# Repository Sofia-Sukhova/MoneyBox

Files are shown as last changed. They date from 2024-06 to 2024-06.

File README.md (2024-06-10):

# MoneyBox :coin: 
### Команда

Бочкарев Федор - электроника и ПО

Бочкарева Софья - проектирование и 3D моделирование

## Цель
Построить копилку с автоматическим определением номинала монет и накоплением общей суммы.

## Решение
Корпус копилки состоит из двух частей - короба для монет и крышки, на которой закреплены все основные детали механизма.

Общая схема определения номинала монеты: монета попадает в щель монетоприемника и перекрывает инфракрасный сигнал светодиода, управляющий фототранзистором. Фототранзистор посылает сигнал на шаговый мотор, присоединенный к клину, закрывающему щель монетоприемника.
Клин отводится на расстояние, соответствующее заданным номиналам монеты, и как только монета падает в щель, фоторанзистор получает сигнал инфракрасного светодиода. Так определяется номинал монеты.

Визуализация данных осуществляется с помощью 4-х строчного дисплея в двух режимах, которые переключаются кнопкой: отображение общей суммы и отображение распределения по номиналам. Также предусмотрен сброс суммы в ноль с помощью кнопки reset. 

Питание осуществляется от сети постоянного тока 5V 

### Компоненты и технологии

* Корпус, крышка и детали механизма затвора (клин-задвижка и поворотное кольцо) напечатаны из PETG пластика на 3D принтере.

* Для электрической части использованы 
  * Arduino Nano
  * Шаговый мотор
  * LCD дисплей 2004 с модулем I2C 
  * плата-драйвер мотора
  * фототранзистор
  * ИК светодиод

### Проблемы и трудности

Основная проблема заключалась в ошибках проектирования корпуса и крышки, которые были выявлены во время тестирования устройства.

## Тестирование устройства

https://github.com/Sofia-Sukhova/MoneyBox/assets/80464142/ff9c0ffd-643b-4358-b3ea-821b1e63e1c1

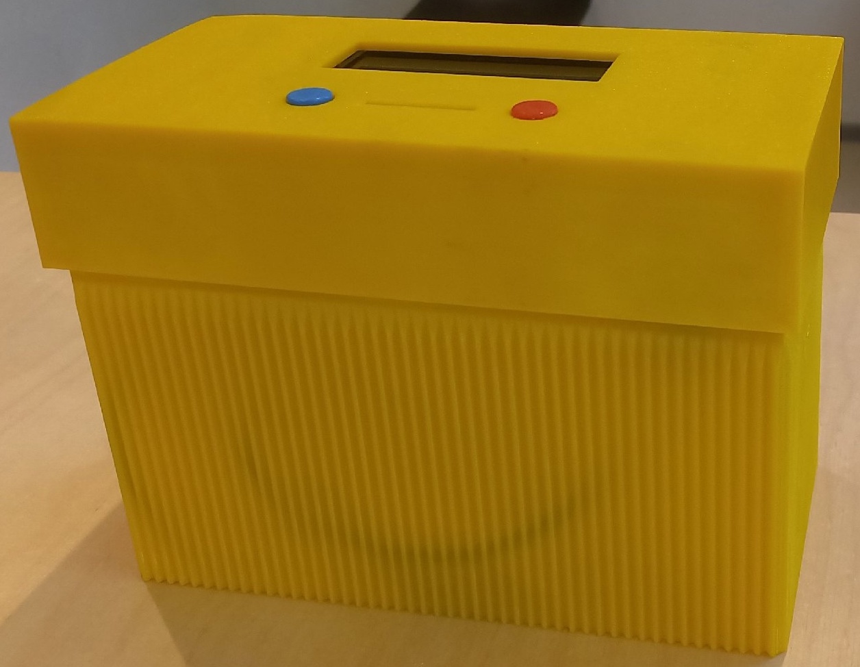
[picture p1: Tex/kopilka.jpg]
Фото готовой копилки снаружи


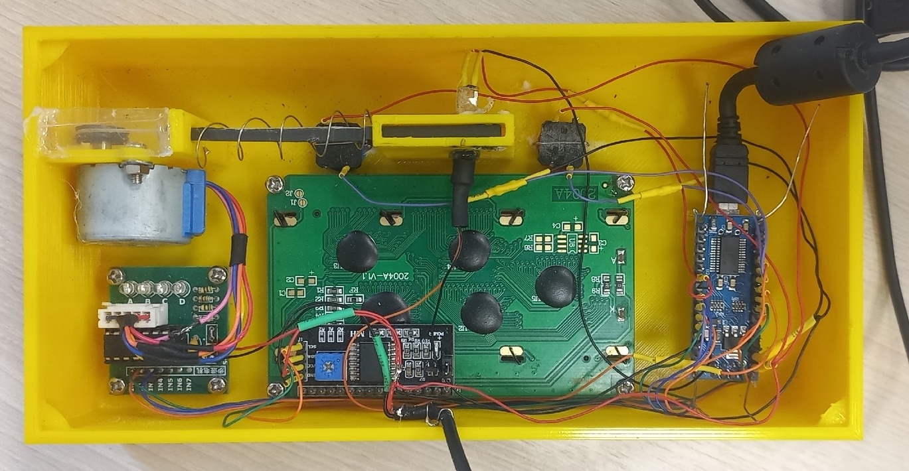
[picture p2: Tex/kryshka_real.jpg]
Фото готовой копилки внутри


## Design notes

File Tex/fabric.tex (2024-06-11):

\subsection{Изготовление и сборка.}

Все детали были изготовлены на 3д принтере. Изначально коробка была сделана без ребер жесткости, из-за чего при печати она деформировалась. Поэтому мы изменили конструкцию коробки, добавив ребра жесткости. 
\par\medskip

\begin{figure}[H]
	\centering
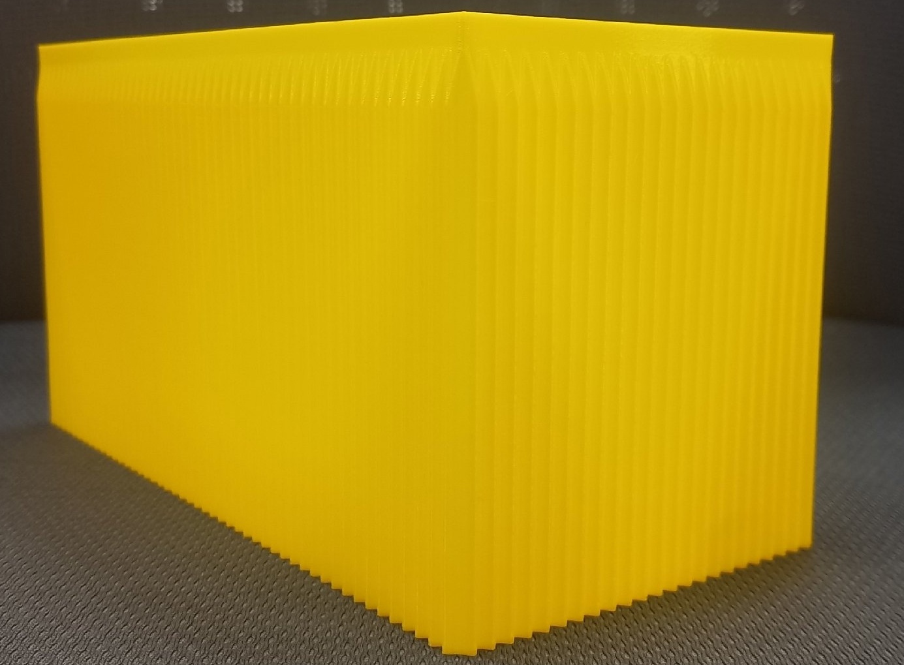
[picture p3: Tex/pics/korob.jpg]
	
	\caption{Короб для монет}
	\label{ris:korob_done}
\end{figure}

Электрическая схема была собрана из: шагового мотора, платы-драйвера шагового мотора, Arduino Nano, фототранзистора, ИК-светодиода, LCD экрана формата 2004 вместе с платой I2C, 2-х кнопок и провода USB (для питания). Схема соединений приведена ниже на рисунке~\ref{ris:scheme_electric}.

\begin{figure}[H]
	\centering
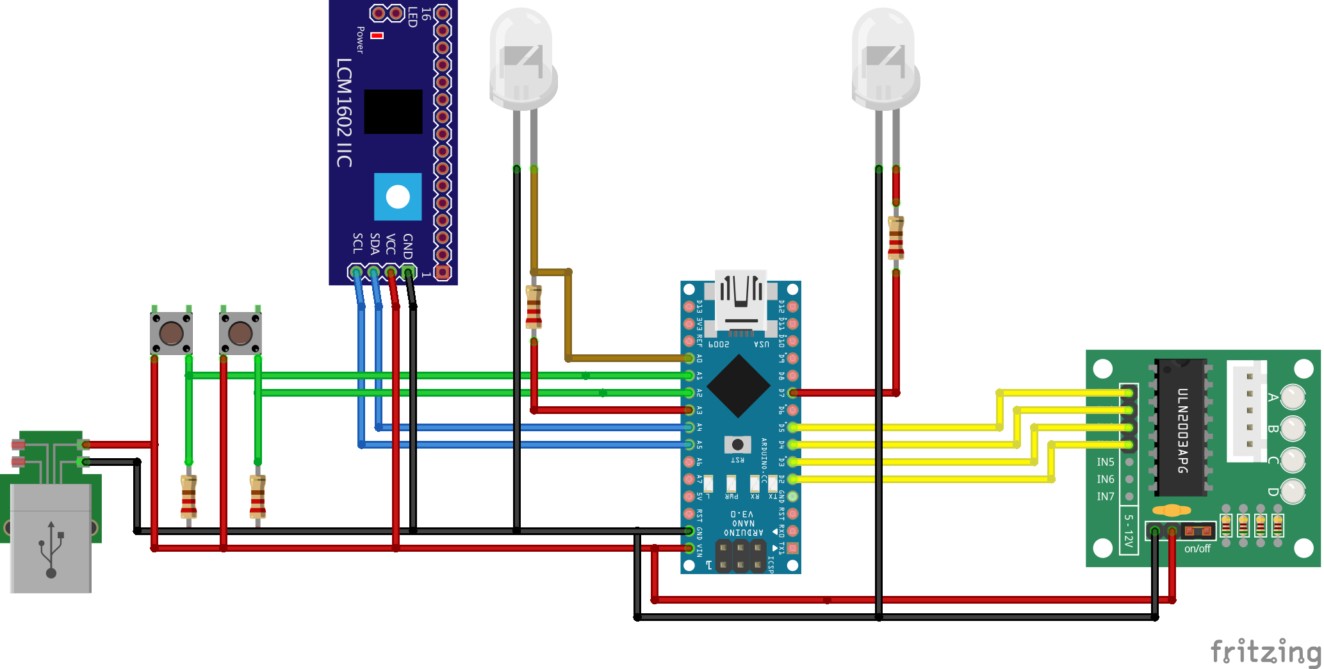
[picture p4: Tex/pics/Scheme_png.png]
	
	\caption{Схема соединения проводов}
	\label{ris:scheme_electric}
\end{figure}

При сборке были исправлены выявленные ошибки моделирования. В основном это касается отсутствующего отверстия для щели под ИК-светодиод и фототранзистор.
\par\medskip

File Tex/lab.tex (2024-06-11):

\documentclass[a4paper,12pt]{extarticle}	% Стиль
%\usepackage[pdftex,unicode,colorlinks=true,linkcolor = blue]{hyperref}

\usepackage{graphicx}
\usepackage{wrapfig}

\usepackage{rotating}

\usepackage{mathtext}
%\usepackage{autonum}

\usepackage{multirow}

\usepackage{caption}

\usepackage{float}

\usepackage{enumitem}
\usepackage{hyperref}
\usepackage[rgb]{xcolor}
\hypersetup{ % Гиперссылки
	colorlinks=true, % false: ссылки в рамках
	urlcolor=blue, % на URL
    linkcolor=blue,
	citecolor=blue,
    filecolor=blue 
}

\usepackage[T2A]{fontenc}
\usepackage[utf8]{inputenc}
\usepackage[english,russian]{babel}

\usepackage{amsmath,amsfonts,amssymb,amsthm,mathtools}

\usepackage{indentfirst} % Красная строка

\newenvironment{comment}{}{}

\graphicspath {{ Images / }}

\usepackage{listings}             % Include the listings-package
\lstset{language=[ANSI]C}
\lstset{numbers=left, stepnumber=1}

\bibliographystyle{gost-numeric.bbx}
\usepackage[hyperref=true,bibencoding=utf8,bibstyle=gost-numeric,sorting=none]{biblatex}
\addbibresource{refs.bib}
\DeclareFieldFormat{url}{\href{#1}{\mkbibacro{URL}}}

\usepackage[left=2cm,right=2cm,top=2cm,bottom=2cm]{geometry}

\begin{document}

	\begin{titlepage}
	\begin{center}
	Физтех-фабрика\\
	\vspace*{5cm}

	\section*{Копилка с автоматическим счётчиком монет}

	\begin{minipage}{0.3\textwidth}
	~
	\end{minipage}
	\hfill
	\begin{minipage}{0.2\textwidth}
		Выполнили:
	\end{minipage}
	\begin{minipage}{0.4\textwidth}
		Бочкарев Федор, Б01-003\\
		Бочкарева Софья, Б01-003
	\end{minipage}

	\begin{flushright}\textbf{\\}\end{flushright}

	\vfill

	Московский физико-технический институт\\
	\the\year{} год

	\end{center}
	\end{titlepage}

	\parindent=0cm
	\parskip=1pt
	\reversemarginpar
	\marginparpush = 0 pt

	\input{intro.tex}
	\input{project.tex}
	\input{fabric.tex}
	\input{progr.tex}
	\input{result.tex}
	\input{links.tex}

\end{document}

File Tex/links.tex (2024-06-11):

\printbibliography[heading=bibnumbered, title=Ссылки.]

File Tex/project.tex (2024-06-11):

\section {Проектирование и изготовление.}

Основные этапы работы:

\begin{itemize}
	\item Проектирование и прототипирование; 
	\item Изготовление деталей;
	\item Сборка;
	\item Разработка управляющей программы
\end{itemize}

\subsection{Проектирование и прототипирование.}

\begin{figure}[H]
	\centering
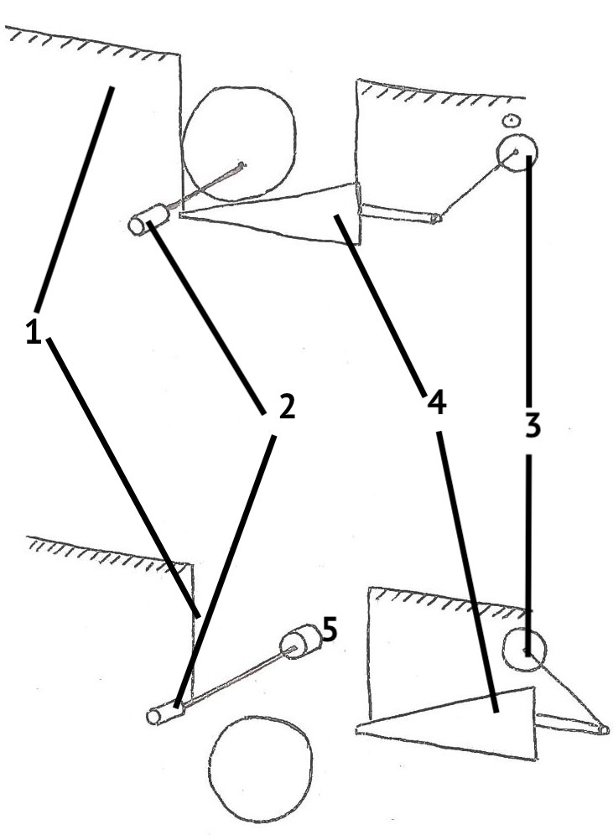
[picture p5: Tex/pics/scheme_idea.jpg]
	
	\caption{Принципиальная схема устройства}
	\label{ris:scheme_idea}
\end{figure}
\par\medskip

Принципиальная схема устройства приведена на рис.~\ref{ris:scheme_idea}. Монета падает в щель монетоприемника 1 и перекрывает инфракрасный луч от инфракрасного светодиода 2. Фоторанзистор 5 передает управляющий сигнал на шаговый мотор 3, который приводит в движение клин 4. Когда клин отводится достаточно для того, чтобы монета упала насквозь, инфракрасный луч светодиода 2 перестает перекрываться, что фиксируется фототранзистором. 
\par\medskip

По данной принципиальной схеме был собран прототип (см. рис.~\ref{ris:proto}). Он успешно прошел проверку на работоспособность, что позволило нам использовать данный механизм в дальнейшем.

\begin{figure}[H]
	\centering
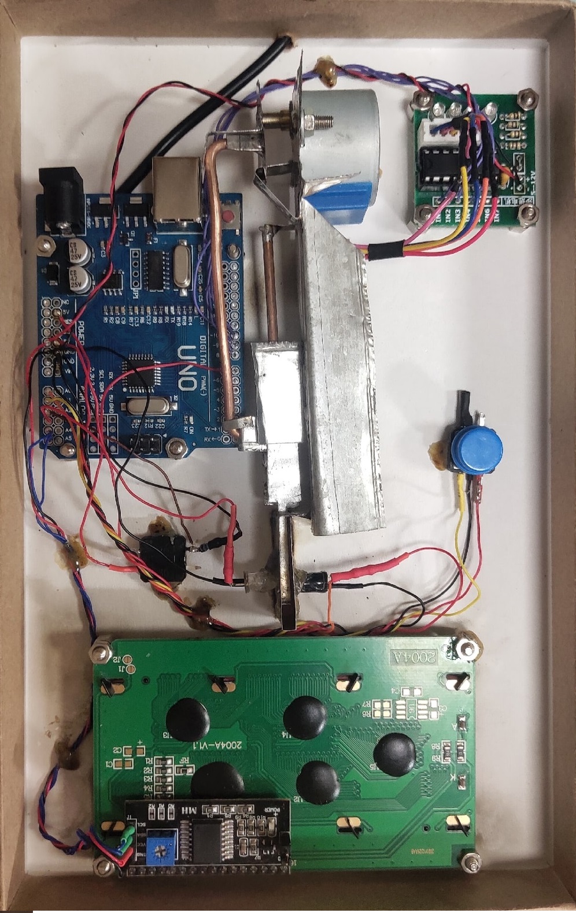
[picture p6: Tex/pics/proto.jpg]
	
	\caption{Прототип}
	\label{ris:proto}
\end{figure}
\par\medskip

При проектировании финальной версии мы доработали механизм затвора для его длины (со 120 мм до 60 мм) (см. рис.~\ref{ris:mechan}). Корпус копилки состоит из двух основных составных частей - крышки, на которой закреплены все основные детали механизма, и коробки для монет. 

\begin{figure}[H]
	\centering
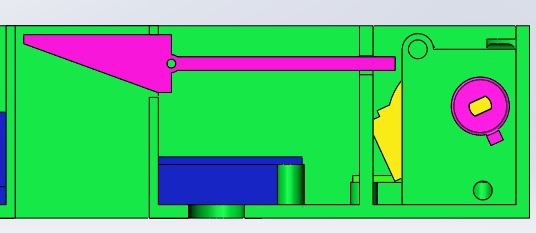
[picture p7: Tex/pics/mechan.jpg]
	
	\caption{Реализация механизма}
	\label{ris:mechan}
\end{figure}
\par\medskip

На верхней крышке предусмотрено размещение 2-х кнопок, дисплея, модуля Arduino Nano, драйвера шагового мотора и его драйвера, фототранзистора и инфракрасного светодиода и механизма затвора. Питание осуществляется от постоянного тока 5V от сети (см. рис.~\ref{ris:kryshka_model}, рис.~\ref{ris:kryshka_real}).  

\begin{figure}[H]
	\centering
	
	\caption{Крышка -- реализация}
	\label{ris:kryshka_real}
\end{figure}
\par\medskip

\begin{figure}[H]
	\centering
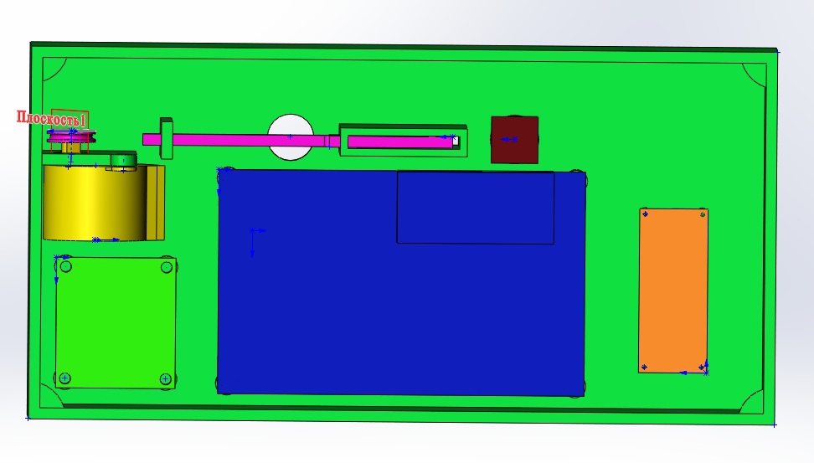
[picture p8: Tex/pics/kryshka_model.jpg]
	
	\caption{Крышка -- модель}
	\label{ris:kryshka_model}
\end{figure}
\par\medskip

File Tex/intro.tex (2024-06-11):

\section {Введение.}

На сегодняшний день большинство транзакций и расчётов происходит путём переводов из мобильных приложений, либо по бесконтактной оплате. Несмотря на рост безналичных платежей, мелкие монеты все еще остаются частью повседневных расчетов. Накоплениеи мелочи может мешать людям своим неопределённым положением -- мелочь лежит где-то на столе, в различных кармах. Организация копилки определит конкретное место для скопившейся мелочи и поможет вернуть её в оборот.
\par\medskip

Исходя из этих соображений, была выдвинута цель.

\section{Цель.}

Построить копилку с автоматическим определением номинала монет и накоплением общей суммы.

\subsection*{Задачи:}
\begin{itemize}
	\item Анализ существующих решений;
	\item Проектирование и изготовление устройства;
	\item Проверка и верификация надёжности работы
\end{itemize}

\section {Анализ существующих аналогов.}

Основными способами определять номинал монеты является определение одного из трёх характерных параметров: диаметр, толщина или магнитные свойства. 
\par\medskip

Определение номинала по магнитным свойствам возможно только с очень чувствительными (дорогими) датчиками.
\par\medskip

Определение номинала по толщине требует высокой точности -- до 0,01 мм. К тому же монета 50 копеек и 1 рубль имеют одинаковую толщину, что делает невозможным одновременный счёт в одном устройстве и копеек и рублей.
\par\medskip

Разница в диаметре различных монет составляет минимум 1 мм. Поэтому реализовать механизм определения номинала монеты целесообразнее именно по диаметру.
\par\medskip

Копилки со счетчиками монет не являются чем-то новым, они уже продаются в различных вариациях, однако такие устройства либо не являются автоматическими и требуют ручного ввода добавленной суммы (пример \cite{Ozon_manual_work}); либо их цена сильно завышена \cite{Ali_auto_work} (стоит отметить, что всевозможные конструкционные решения уже реализованны в широком классе устройств \cite{Cassida}, \cite{Sort_Cassida}, которые специализируются на крупном монетно/денежном обороте, что характерно для банковского сектора, предпринимателей).
\par\medskip

Помимо счётчиков, существуют ещё сортировщики монет, которые достаточно быстро разделяют монеты по номиналу на разные отсеки (примеры: \cite{Sort_Cassida},\cite{Sort_hill},\cite{Sort_default}). Все они имеют схожий механизм работы: монеты скатываются по определённой дорожке и разделяются в процессе движения. Любой подобный сортировщик можно модернизировать: добавить датчики на обнаружение проскакивания монеты на каждый из отсеков разделения и соединить все эти датчики с счётчиком монет -- получится необходимая нам копилка. К сожелению, все подобные сортировщики имеют большие размеры, что является недостатком -- копилка не должна занимать много места.
\par\medskip

Наиболее подходящим будет являтся пример устройста \cite{Gyver} -- диаметр определяется по интенсивности инфракрасного сигнала, приходящего на фоточувствительный элемент (фототранзистор); монеты перекрывают часть ИК-излучения и это изменение регистрирует датчик. Такая реализация допускает возможность ошибки за счет проскакивания монеты и неправильного считывания ее диаметра (к тому же в этой версии не предусмотрены удобные элементы управления).
\par\medskip

\section {Общее описание.}

Исходя из анализа существующих решений, можно составить требования к нашей копилке-счётчику: без сортировки, только автоматический счёт, высокая надёжность, низкая вероятность ошибки, компактность, удобство использования, хороший дизайн.
\par\medskip

Основу надёжного механизма будет составлять не просто щель, а щель с внутренней задвижкой -- такая конструкция не допустит проскакивания монеты без корректного считывания. К тому же, основным измерительным устройством в копилке будет сама щель с задвижкой -- отклонившись на определённую величину, через задвижку проскочат только те монеты, диаметр которых меньше этой величины. Расширяя щель поочерёдно от меньшего диаметра к большему, на каждом отколнии можно определить прошла ли монета или нет, и, в зависимости от итогового отклонения, определять какой был номинал у выпавшей монеты.
\par\medskip

За движение задвижки будет отвечать шаговый мотор. Тем самым, измерение с какого-либо датчика перекладывается на установление заданного угла шагового мотора. Фототранзистор и ИК-светодиодом также установлены в щель -- их задача определять, есть ли в щели монета. Именно фототранзистор и ИК-светодиод будут задавать начало измерения номинала монеты и постепенное открытие щели, а также поределять момент проскакивания монеты при открывании щели.
\par\medskip

Для удобства эксплуатации данные о принятых монетах выводятся на дисплей в двух режимах: общая сумма в копилке и распределение содержимого по номиналам. Управление копилкой осуществляется через 2 кнопки.
\par\medskip

Питание всей электроники осуществело от 5 вольт постоянного тока по кабелю USB.

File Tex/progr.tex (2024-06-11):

\subsection{Разработка управляющей программы.}

Основу прошивки Arduino Nano составляют добавленные библиотеки.

\begin{lstlisting}[frame=single]
#include <GyverStepper.h>
#include <EEPROM.h>
#include <PinChangeInterrupt.h>
#include <string.h>
#include <LiquidCrystal_I2C.h>
\end{lstlisting}

В дальнейшем, весь код можно разделить на части:

\begin{itemize}
	\item Объявление констант, классов, переменных и дефайнов;
	\item Основная работа;
	\item Функции/код связанные с экраном и его выводом;
	\item Функции связанные с записью количества монет в энергонезависимую EEPROM память;
	\item Обработка клафиш управления
\end{itemize}

Вся основная работа заключена в простой алгоритм: постоянно считывается данные с сенсора (фототранзистора), если они превысили определенный порог (сенсор заслонили от ИК), то у нас монетка и нужно отодвигать защёлку путём поворота шагового мотора. Для каждой монетки существует соответствующий угол, который напрямую связан с диаметром монеты. Зная на каком углу датчик вновь увидел ИК мы можем определить какая это монета.

\begin{lstlisting}[frame=single]
void loop {
	data = analogRead();
	if (data > BORDER) {
		if      (check(...)){this_coin = 0}
		else if (check(...)){this_coin = 1}
		...
	}
}
\end{lstlisting}

Из вышеприведённой вставки, главная функция имеет следующий функционал: поворачивается на определённый угол $R$, затем даёт время на возможный сброс монетки и срабатывание датчика $Y$, потом вновь считывает датчик и определяет -- упала ли монета или нет. 
\par\medskip

\begin{lstlisting}[frame=single]
bool check(int * mass, int R, int Y){
	int data = analogRead(inSEN);
	if (data > 100) {
		my_rotate(R);
	} else {
		comeback();
		return 1;
	}
	delay(Y);
	return 0;
}
\end{lstlisting}
Если монета была сброшена, то эта функция прорутит мотор до стопора, тем самым вернув защёлку в полностью закрытое состояние.
\par\medskip

По результату выхода из этой функции определяется тип монетки и он записывается в буффер имеющихся монет.
\par\medskip

По данным этого буффера на экран выводиться сумма и количество монет по номиналам.
\par\medskip

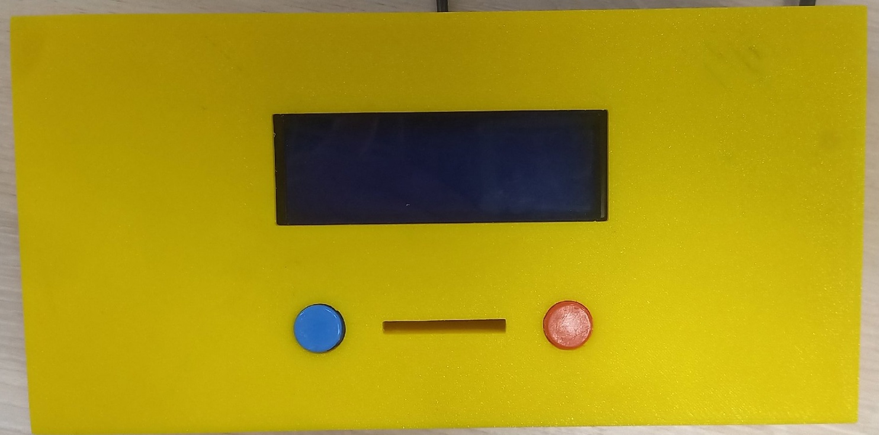
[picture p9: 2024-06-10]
Tex/pics/kryshka_face_real.jpg

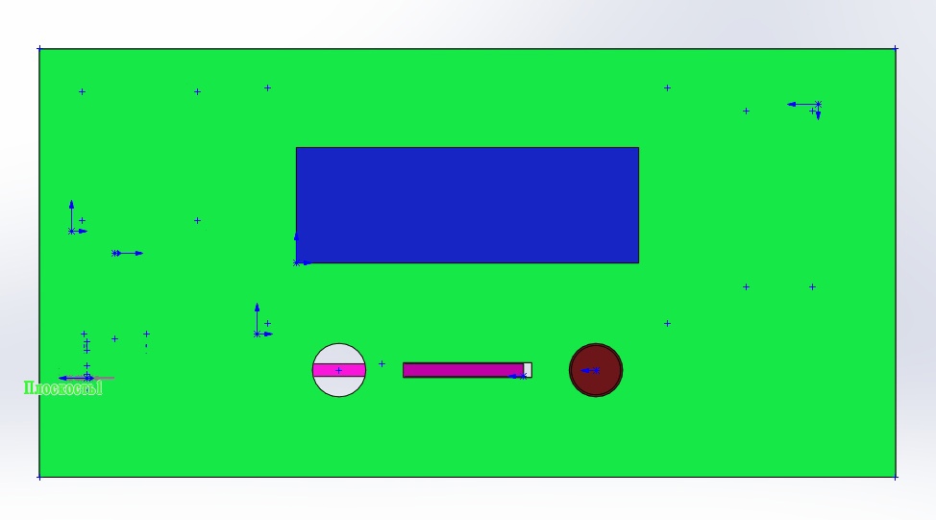
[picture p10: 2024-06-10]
Tex/pics/kryshka_face_model.jpg

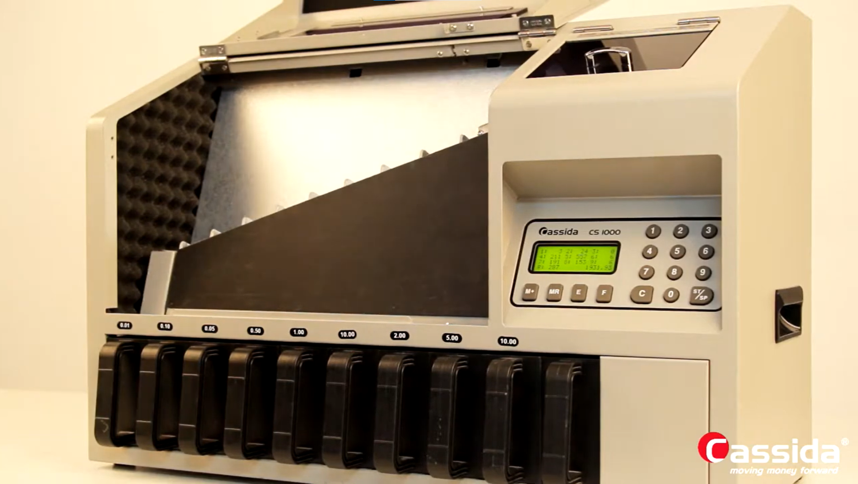
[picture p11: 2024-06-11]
Tex/pics/Cassida_sorting.png

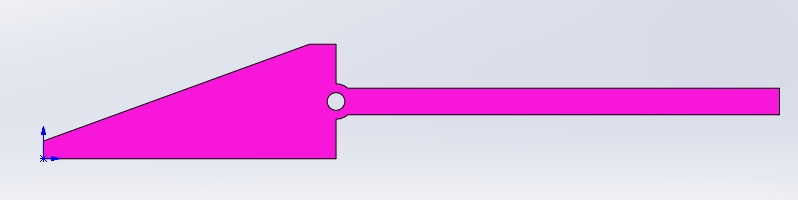
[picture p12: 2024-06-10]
Tex/pics/klin.jpg

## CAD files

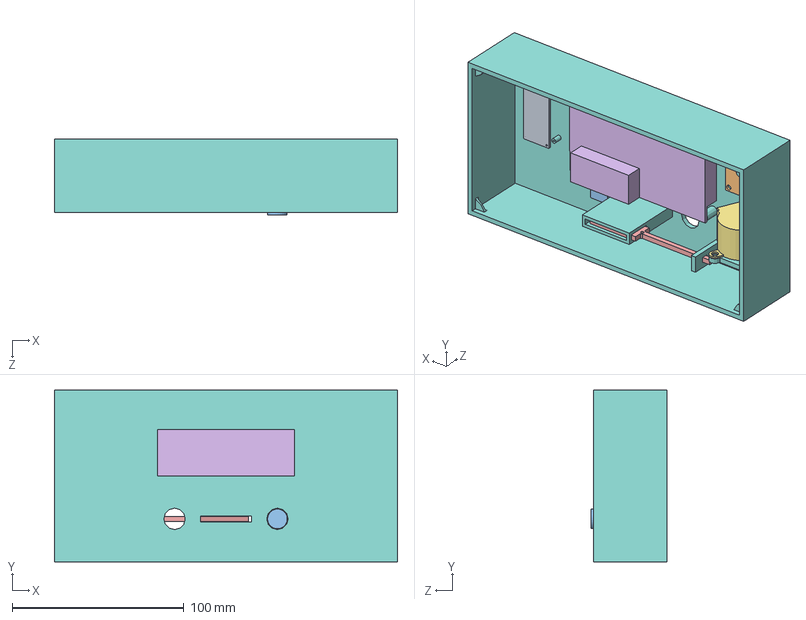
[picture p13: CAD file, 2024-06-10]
CAD/Сборка.SLDASM
200.0 x 100.0 x 44.5 mm
Крышка
Мотор
Экран
Клин
Колечко
Кнопка
Плата-драйвер
Плата-ардуино

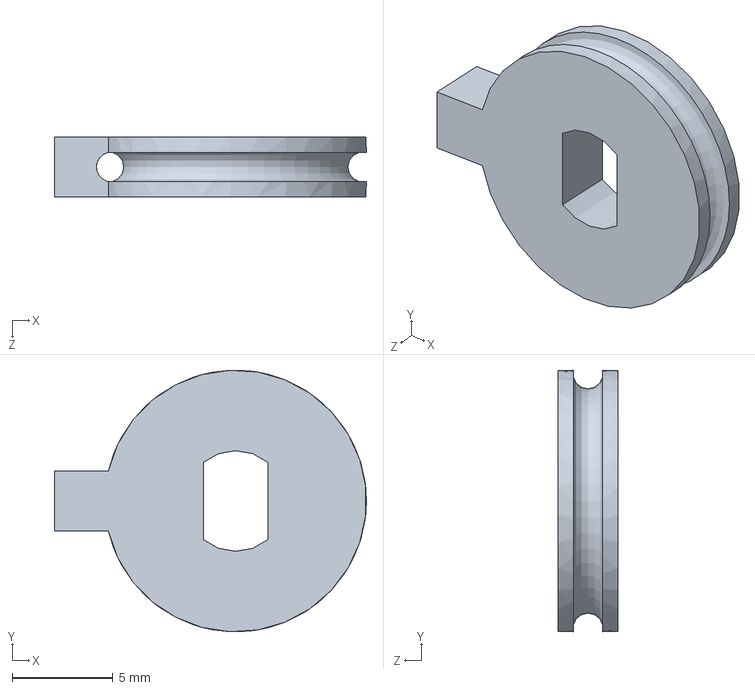
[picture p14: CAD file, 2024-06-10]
CAD/Колечко.SLDPRT
15.5 x 13.0 x 3.00 mm

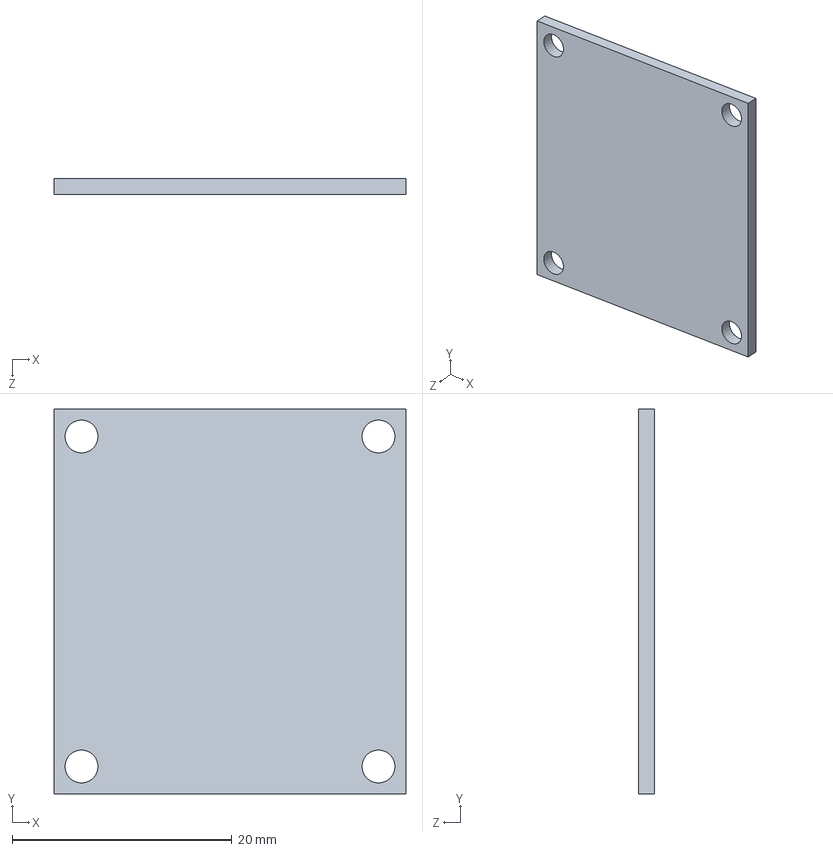
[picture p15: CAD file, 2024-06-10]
CAD/Плата-драйвер.SLDPRT
32.0 x 35.0 x 1.50 mm

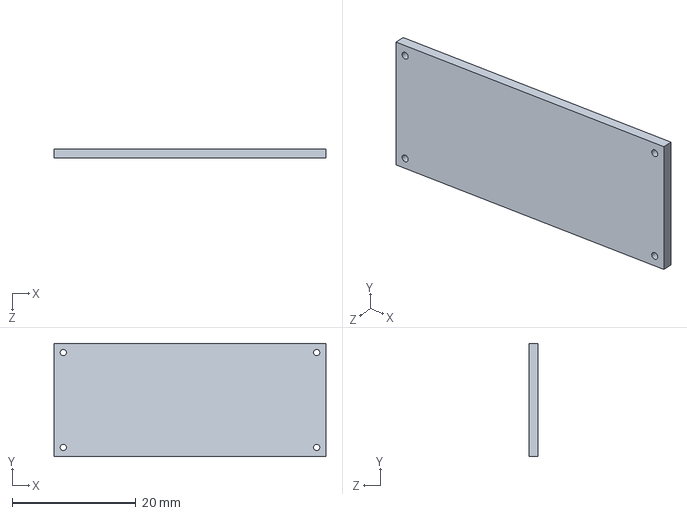
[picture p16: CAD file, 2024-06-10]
CAD/Плата-ардуино.SLDPRT
44.0 x 18.4 x 1.50 mm

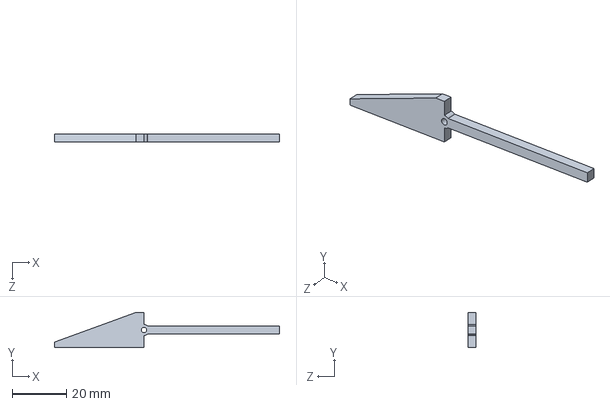
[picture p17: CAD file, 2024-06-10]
CAD/Клин.SLDPRT
83.0 x 12.9 x 3.00 mm

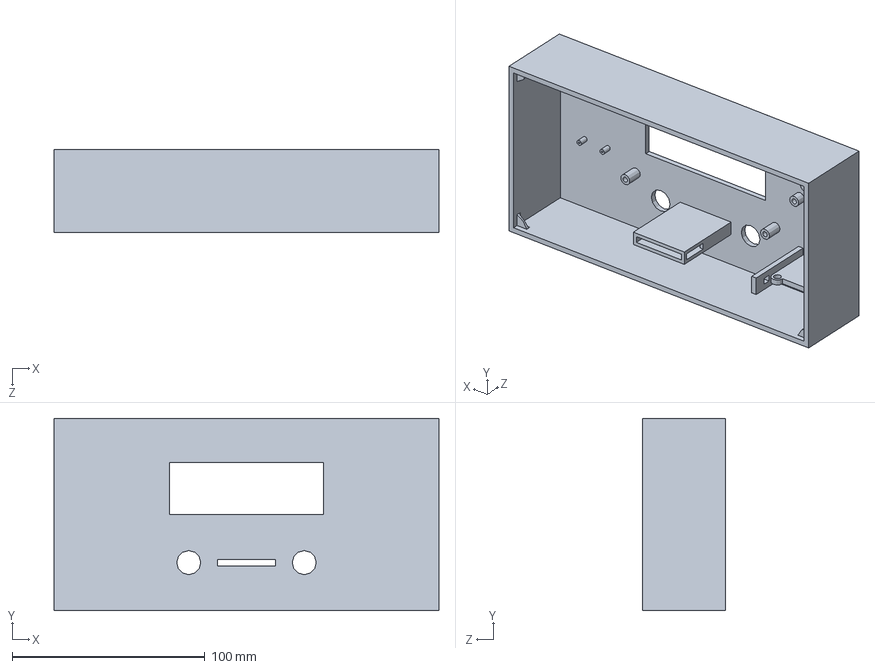
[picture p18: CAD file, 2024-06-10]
CAD/Крышка.SLDPRT
200.0 x 100.0 x 43.0 mm

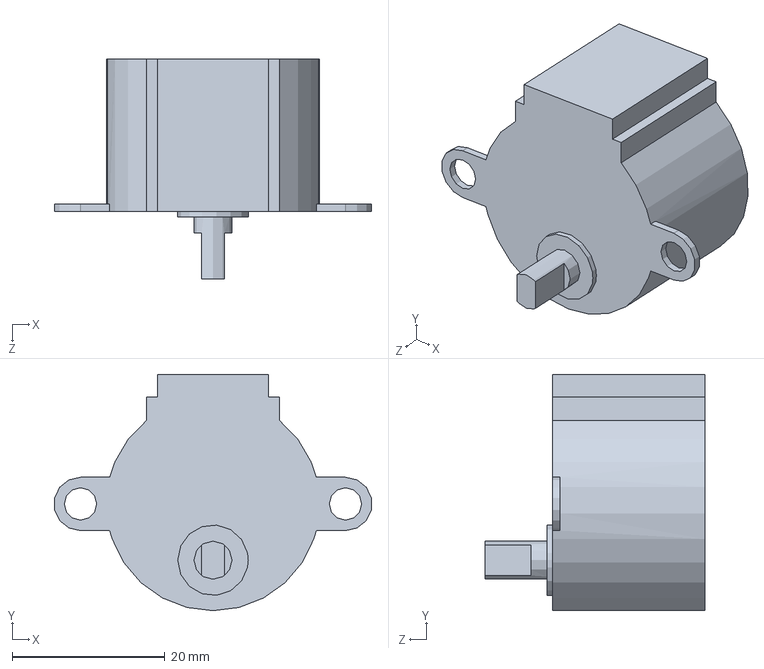
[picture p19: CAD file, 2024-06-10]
CAD/Мотор.SLDPRT
41.6 x 31.0 x 28.9 mm

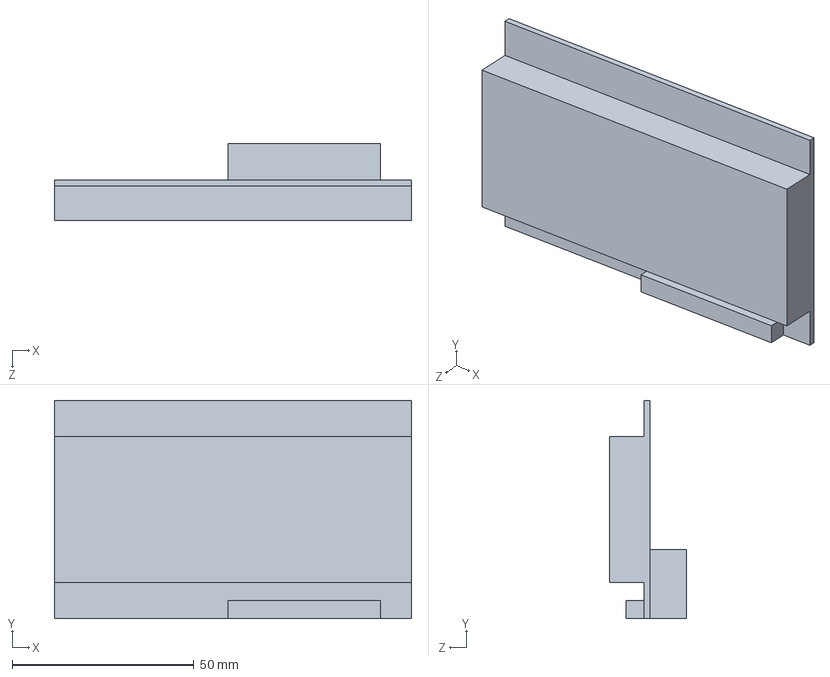
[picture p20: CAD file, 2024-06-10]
CAD/Экран.SLDPRT
98.2 x 60.1 x 21.2 mm

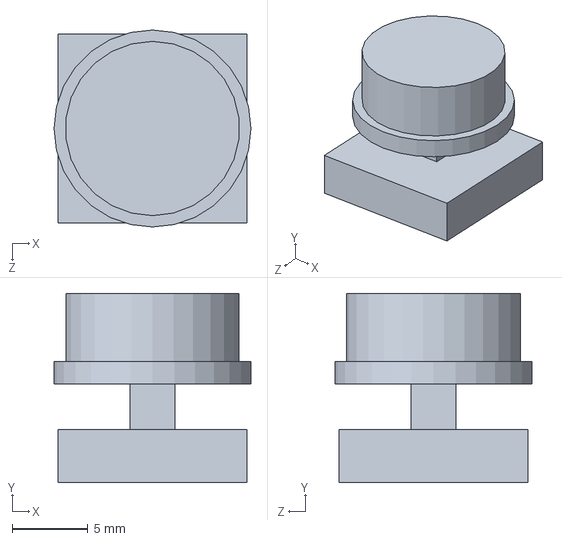
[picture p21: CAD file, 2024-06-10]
CAD/Кнопка.SLDPRT
13.0 x 12.5 x 13.0 mm

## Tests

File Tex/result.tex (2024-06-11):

\section {Тестирование.}

Основными задачами тестирования были проверка надежности механизма и калибровка шагового мотора для корректного определения каждого номинала.
\par\medskip

Проверка включала в себя ручной пересчёт монет и автоматический с помощью копилки. Итоговый результат откалиброванной копилки-счётчика полностью совпал по всем номиналам с ручным счётом. В ходе тестирования было считано:
\begin{itemize}
	\item 12 монет по 10 рублей;
	\item 56 монет по 5 рублей;
	\item 97 монет по 2 рубля;
	\item 170 монет по 1 рублю;
	\item 31 монета 50 копеек;
	\item 34 монет 10 копеек;
	\item 5 монет по 5 копеек;
	\item 0 монет по 1 копейке
\end{itemize}

В процессе тестирования были выявлены и исправлены некоторые недостатки модели. Выявилось, что шаговый мотор может перейти стопорное положение (упор в корпус) и тем самым деформировать стенку корпуса. Также была многократно доработана система задвижки -- были выбраны 2 наиболее подходящие пружины из порядка 20, и одна из них была дополнительно деформирована для достижения надёжной работы механизма.

\section {Результаты.}

Было спроектировано, изготовлено и протестировано устройство — копилка со счетчиком монет. Функционально устройство работает исправно. 
\par\medskip

Документация и файлы прошивки, моделей CAD расположены на GitHub \cite{github}.
\par\medskip

В качестве дальнейшего развития можно доработать управляющую программу и внедрить в нее новые функции, а также доработать модель и исправить недостатки, выявленные при тестировании модели.

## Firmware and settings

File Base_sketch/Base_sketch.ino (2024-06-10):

#include <GyverStepper.h>
#include <EEPROM.h>
#include <PinChangeInterrupt.h>
#include <string.h>
#include <LiquidCrystal_I2C.h>
GStepper<STEPPER4WIRE> stepper(2048, 5, 3, 4, 2);
LiquidCrystal_I2C lcd(0x27,20,4);

#define inSEN A0
#define outSEN A3
#define led 7
#define button A2
#define pin_to_reset_sum A1

#define TIME_TO_FALL 50
#define TIME_TO_CHECK 0
#define COUNT_TO_REFRESH 100

const int border = 10;
const int max_step = 20;

int data;

volatile int flag = 0;

int money[9] = {0}; // 8 монет, 9 - для отработки ошибокы

#define VALUE_FOR_1_K   -100 
#define VALUE_FOR_10_K  -850
#define VALUE_FOR_5_K   -60
#define VALUE_FOR_50_K  -50
#define VALUE_FOR_1_R   -65
#define VALUE_FOR_10_R  -40
#define VALUE_FOR_2_R   -80
#define VALUE_FOR_5_R   -200

#define RETURN VALUE_FOR_1_K + VALUE_FOR_10_K + VALUE_FOR_5_K + VALUE_FOR_50_K + VALUE_FOR_1_R + VALUE_FOR_2_R + VALUE_FOR_5_R + VALUE_FOR_10_R - 100

#define TARGER_MESSAGE "Budget"

int current_screen = 0;
int change_screen = 0;
int refresh = 0;

uint8_t attachPCINT(uint8_t pin) {
  if (pin < 8) {            // D0-D7 (PCINT2)
    PCICR |= (1 << PCIE2);
    PCMSK2 |= (1 << pin); return 2; } else if (pin > 13) {    //A0-A5 (PCINT1)
    PCICR |= (1 << PCIE1);
    PCMSK1 |= (1 << pin - 14);
    return 1;
  } else {                  // D8-D13 (PCINT0)
    PCICR |= (1 << PCIE0);
    PCMSK0 |= (1 << pin - 8);
    return 0;
  }
}

ISR(PCINT1_vect) {  // пины A0-A5
  flag = 1;
}

void my_rotate(int R, int W) {
  stepper.setTarget(R , RELATIVE);

  for (int i = 0; i < abs(R) * 2; i++){
    stepper.tick();
    delay(1);
  }
  delay(W);
}

void comeback() {
  stepper.setTarget(abs(RETURN));

  for (int i = 0; i < 2* abs(RETURN); i++){
    stepper.tick();
    delay(1);
  }
}

bool check(int * mass, int R, int W, int Y){
  int data = analogRead(inSEN);
  if (data > 100) {
      my_rotate(R, W);
    } else {
      comeback();
      return 1;
    }
    delay(Y);
    return 0;
}

float cal_sum (){
  return money[0]*0.01 + money[1]*0.05 + money[2]*0.1 + money[3]*0.5 + money[4] + money[5]*2 + money[6]*5 + money[7]*10;
}

void sc_greeter(){
  lcd.clear();
  lcd.setCursor(10-strlen(TARGER_MESSAGE)/2,0);
  lcd.print(TARGER_MESSAGE);
  
  String sum(cal_sum(), 2);

  lcd.setCursor(10-sum.length()/2,1);
  lcd.print(sum);
}

void sc_counter(){
  lcd.clear();
  lcd.setCursor(0,0);
  lcd.print("0.01-");
  lcd.print(money[0]);
  lcd.setCursor(0,1);
  lcd.print("0.05-");
  lcd.print(money[1]);
  lcd.setCursor(0,2);
  lcd.print(" 0.1-");
  lcd.print(money[2]);
  lcd.setCursor(0,3);
  lcd.print(" 0.5-");
  lcd.print(money[3]);
  lcd.setCursor(10,0);
  lcd.print(" 1-");
  lcd.print(money[4]);
  lcd.setCursor(10,1);
  lcd.print(" 2-");
  lcd.print(money[5]);
  lcd.setCursor(10,2);
  lcd.print(" 5-");
  lcd.print(money[6]);
  lcd.setCursor(10,3);
  lcd.print("10-");
  lcd.print(money[7]);
}

void setup() {    
  EEPROM.get(0, money);

  lcd.init();                       //  Инициируем работу с LCD дисплеем
  lcd.backlight();                  //  Включаем подсветку LCD дисплея
  lcd.setCursor(0,0);
  lcd.print("Loading...");
  
  stepper.setRunMode(FOLLOW_POS);
  stepper.reverse(true);
  stepper.setMaxSpeed(500);
  stepper.setAcceleration(0);
  stepper.setTarget(1500);

  pinMode(inSEN, INPUT);
  pinMode(button, INPUT);
  pinMode(pin_to_reset_sum, INPUT);
  pinMode(outSEN, OUTPUT);
  pinMode(led, OUTPUT);

  digitalWrite(outSEN, 1);
  digitalWrite(led, 1);

  attachPCINT(button);

  for (int i = 0; i < 10000; i++){
    stepper.tick();
    delay(1);
  }

  sc_greeter();
  Serial.begin(9600);
}

int counter = 0;
int new_money = 0;

void loop(){
  delay(10);
  data = analogRead(pin_to_reset_sum);

  if(data > 500) {
    memset(money,0,sizeof(money));
    refresh = 1;
  }

  data = analogRead(inSEN);

  counter++;
  if ((counter > COUNT_TO_REFRESH) && (current_screen == 0)) {
    lcd.setCursor(0,3);
    lcd.print("                    ");
  }
  if ((counter > 2 * COUNT_TO_REFRESH) && (current_screen == 0)) {
    lcd.setCursor(0,2);
    lcd.print("                    ");
  }

  if (data > 100) {
    counter = 0;

    int ret = 0;

    if      (check(money, VALUE_FOR_1_K,  TIME_TO_FALL, TIME_TO_CHECK)){refresh = 1;new_money = 0; }
    else if (check(money, VALUE_FOR_10_K, TIME_TO_FALL, TIME_TO_CHECK)){refresh = 1;new_money = 1;money[0]++;}
    else if (check(money, VALUE_FOR_5_K,  TIME_TO_FALL, TIME_TO_CHECK)){refresh = 1;new_money = 3;money[2]++;}
    else if (check(money, VALUE_FOR_50_K, TIME_TO_FALL, TIME_TO_CHECK)){refresh = 1;new_money = 2;money[1]++;}
    else if (check(money, VALUE_FOR_1_R,  TIME_TO_FALL, TIME_TO_CHECK)){refresh = 1;new_money = 4;money[3]++;}
    else if (check(money, VALUE_FOR_10_R, TIME_TO_FALL, TIME_TO_CHECK)){refresh = 1;new_money = 5;money[4]++;}
    else if (check(money, VALUE_FOR_2_R,  TIME_TO_FALL, TIME_TO_CHECK)){refresh = 1;new_money = 8;money[7]++;}
    else if (check(money, VALUE_FOR_5_R,  TIME_TO_FALL + 10, TIME_TO_CHECK)){refresh = 1;new_money = 6;money[5]++;}
    else    {refresh = 1;new_money = 7;comeback();money[6]++;}

    EEPROM.put(0, money);
  }

  if(flag == 1){
    flag = 0;
    delay(500);
    if (flag == 1){
      flag = 0;
      change_screen = 1;
    }
  }

  if ((current_screen == 0 && change_screen == 1) || (current_screen == 1 && refresh == 1)) {
    current_screen = 1;
    change_screen = 0;
    sc_counter(); // это первый режим работы 
  }
  if ((current_screen == 1 && change_screen == 1) || (current_screen == 0 && refresh == 1)) {
    current_screen = 0;
    change_screen = 0;
    sc_greeter(); // это вторый режим работы 
    switch (new_money){
      case 0:lcd.setCursor(5,2);lcd.print("");break;
      case 1:lcd.setCursor(8,2);lcd.print("+0.01");lcd.setCursor(9,3);lcd.print("WOW");break;
      case 2:lcd.setCursor(8,2);lcd.print("+0.05");lcd.setCursor(8,3);lcd.print("good");break;
      case 3:lcd.setCursor(8,2);lcd.print("+0.1"); lcd.setCursor(8,3);lcd.print("cool");break;
      case 4:lcd.setCursor(8,2);lcd.print("+0.5"); lcd.setCursor(8,3);lcd.print("Nice");break;
      case 5:lcd.setCursor(9,2);lcd.print("+1");   lcd.setCursor(7,3);lcd.print("Great!");break;
      case 6:lcd.setCursor(9,2);lcd.print("+2");   lcd.setCursor(6,3);lcd.print("Amazing!");break;
      case 7:lcd.setCursor(9,2);lcd.print("+5");   lcd.setCursor(5,3);lcd.print("Wonderful!");break;
      case 8:lcd.setCursor(9,2);lcd.print("+10");  lcd.setCursor(6,3);lcd.print("PERFECT!");break;
      default:lcd.setCursor(4,2);lcd.print("ERROR DEFAULT");break;
    }
  }
  refresh = 0;
}

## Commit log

2024-06-10 add cad models
    [Клин.SLDPRT, Кнопка.SLDPRT, Колечко.SLDPRT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]
2024-06-10 small changes in CAD files
    [Колечко.SLDPRT]
2024-06-10 remove tex's tresh, reorganize tex, add couple pic
2024-06-11 do remarks
    [Крышка.3MF]
